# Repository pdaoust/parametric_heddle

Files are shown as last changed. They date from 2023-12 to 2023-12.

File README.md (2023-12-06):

# Parametric heddle

A set of OpenSCAD files for generating a weaving loom heddle suitable for 3D printing. This heddle fits nicely into the heddle braces of this [rigid heddle weaving loom on Thingiverse](https://www.thingiverse.com/thing:490467).

You can configure various things like:

* the thickness of the dowel that runs the length of the heddle
* the height of the entire heddle (fun fact: I created these files because the build volume of my printer was slightly too small for the original heddle in the above project)
* the thickness of the reed
* the height of the reed holes
* reed dent count (threads per inch)
* the length of a heddle screen in inches

This design is a bit different from the original:

* The reeds are centred in the panel, so you don't have to worry about whether the file you're printing is a left or a right.
* It's meant to be assembled without screws if you like -- instead, you print out dowel end-caps and pressure-fit them into the screens at the ends of the dowel. There are little notch/tongue fittings to keep the thing from swivelling on the dowel, and to hopefully provide a little more pressure-fitting. (Note that, by default, the end-caps are configured to also have American #3 countersunk screw holes so you can screw them together if you like.)
* Because it's parametric and goes together with pressure fittings, this design is explicitly meant to let you assemble and reassemble variable-dent heddles of whatever configuration you like. Two inches of six-dent followed by one inch of twelve-dent? Go for it!!!
* All pieces are completely symmetrical, so you don't need to generate left and right models.

## Usage

Just open up `heddle.scad`, scroll down to the line where it says to uncomment various lines in order to generate models, and hit F6!. There are preconfigured lines for a heddle screen panel, a top dowel cap, and a bottom dowel cap.

To configure things, read all the documentation in the comments. It's quite well-documented (if you find something doesn't make sense, please open up a GitHub issue!) The parameters you'll probably want to change are `heddle_height`, `reed_dent`, and `screen_inches`.

## Examples

A bottom dowel cap, with #3 screw hole and tongues to fit into the screen handle. This is sized to match the original heddle design, in which the bottom handle pokes out past the last reed by about 8mm.

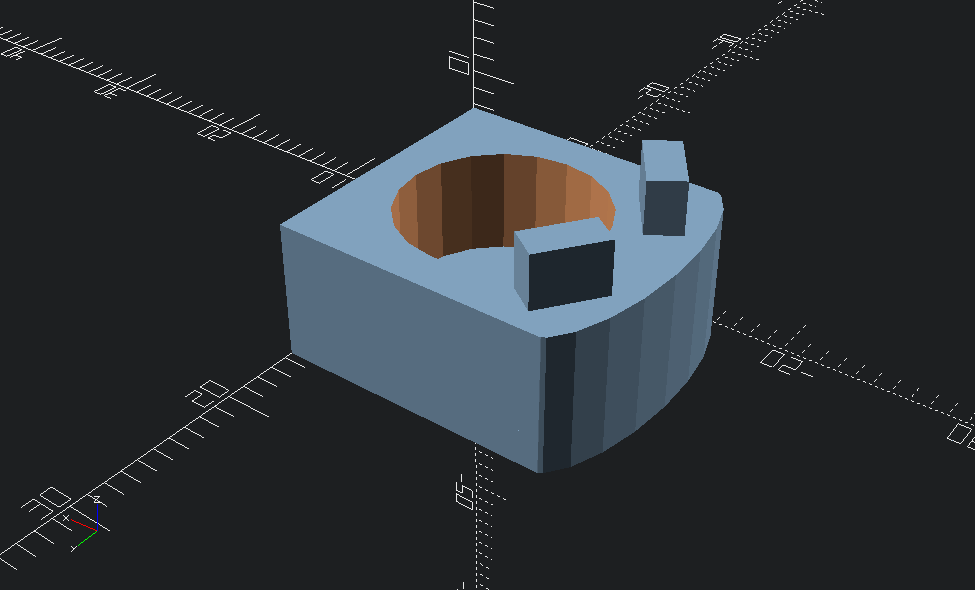
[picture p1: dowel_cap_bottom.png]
dowel cap bottom


A top dowel cap, which is basically just a thin panel with tongues and a screw hole. You might want to screw this one into the dowel if the pressure fitting isn't enough.

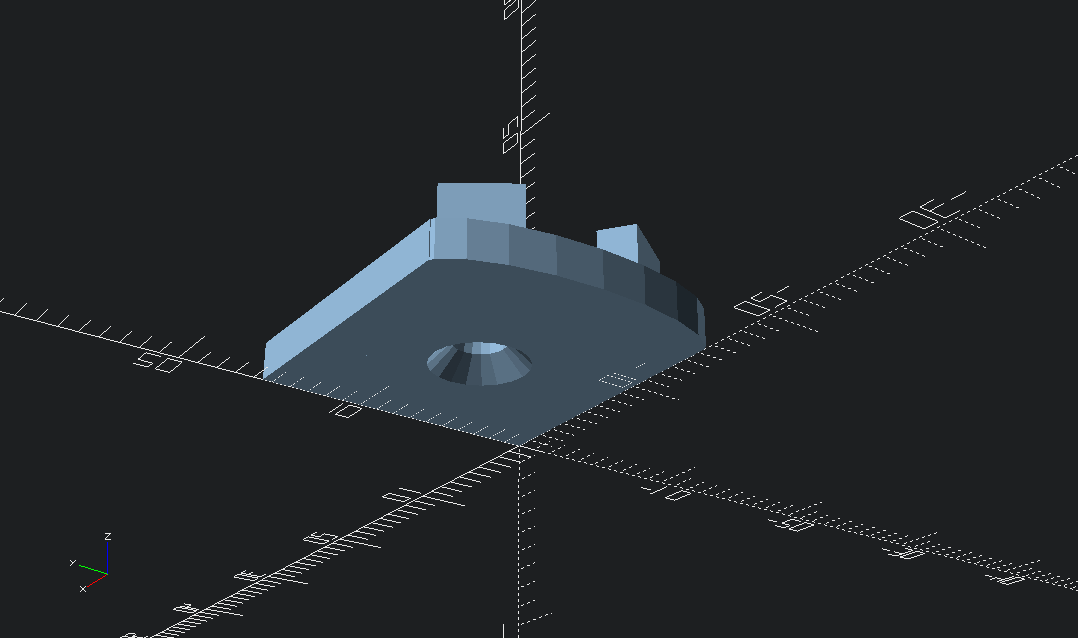
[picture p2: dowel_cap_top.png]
dowel cap top


A 12-dent screen four inches long.

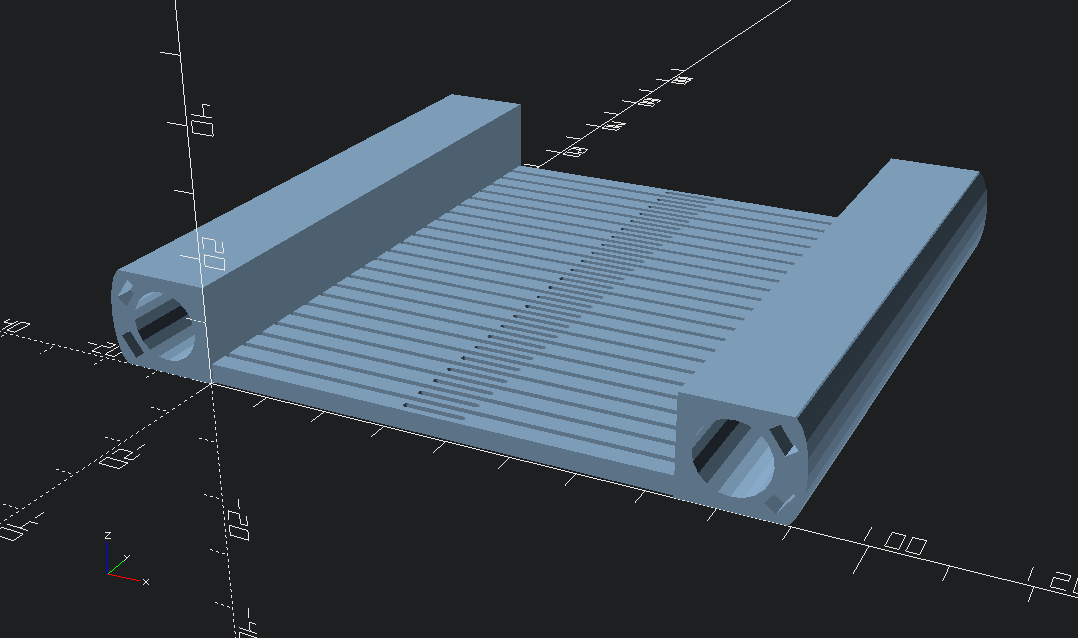
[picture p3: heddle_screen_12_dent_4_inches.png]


An 8-dent screen one inch long.

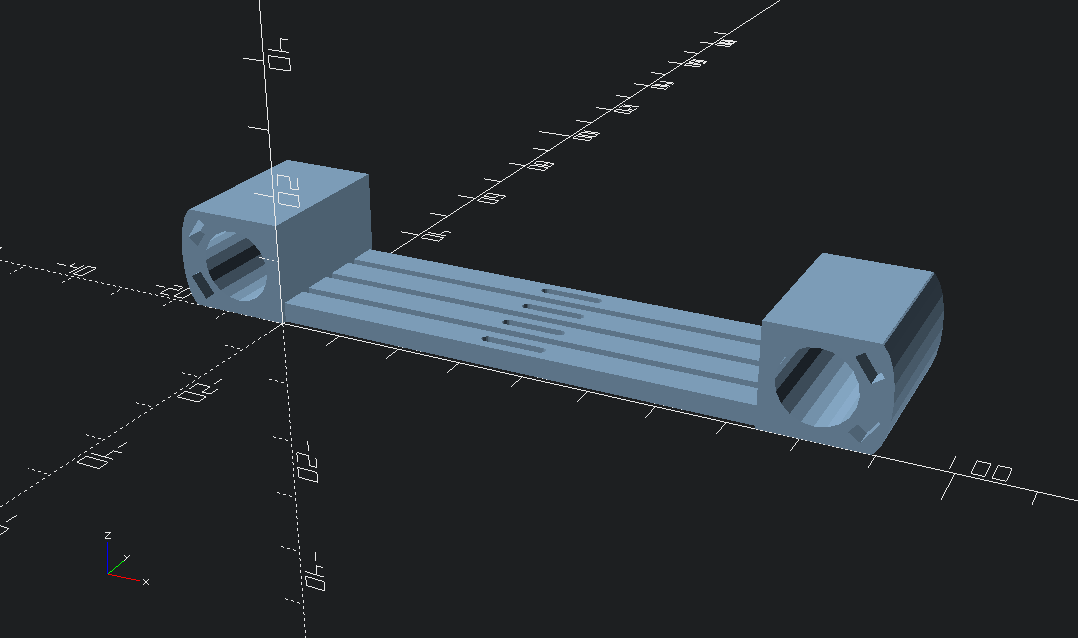
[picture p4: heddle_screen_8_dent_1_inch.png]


An 8-dent screen only 70mm tall and two inches long.

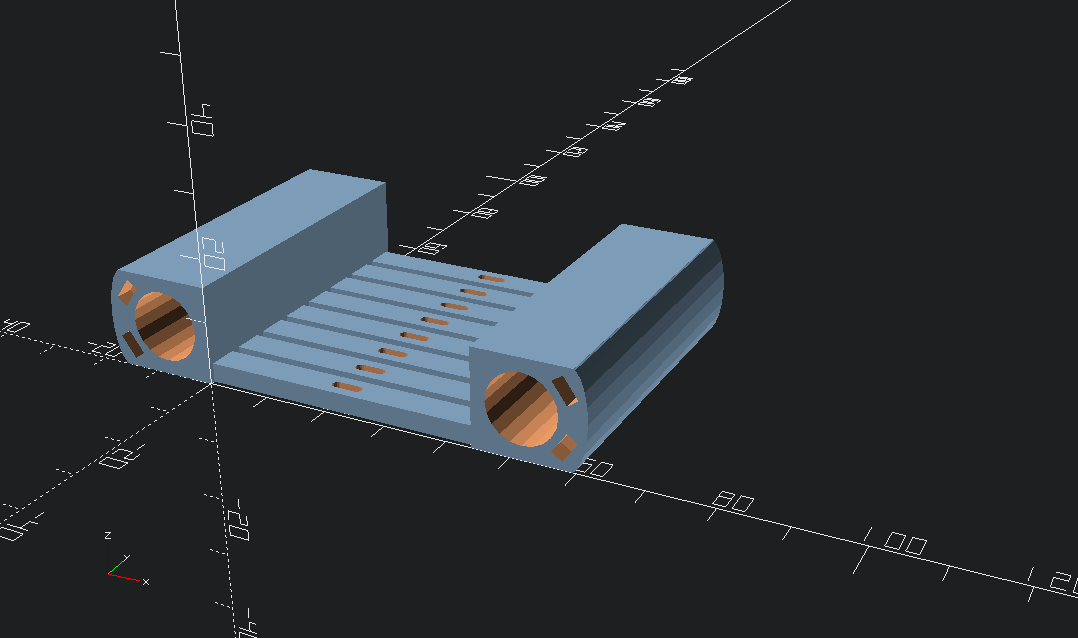
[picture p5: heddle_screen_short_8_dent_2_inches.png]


An 8-dent screen with a fancy band weaving pattern, similar to what you see in [this commercially available heddle](https://harvestlooms.com/products/15-double-slot-rigid-heddle-loom-weaving-backstrap-band-weaving-inkle-pattern-weaving-saami-sami-baltic-nordic-inlay-patterns).

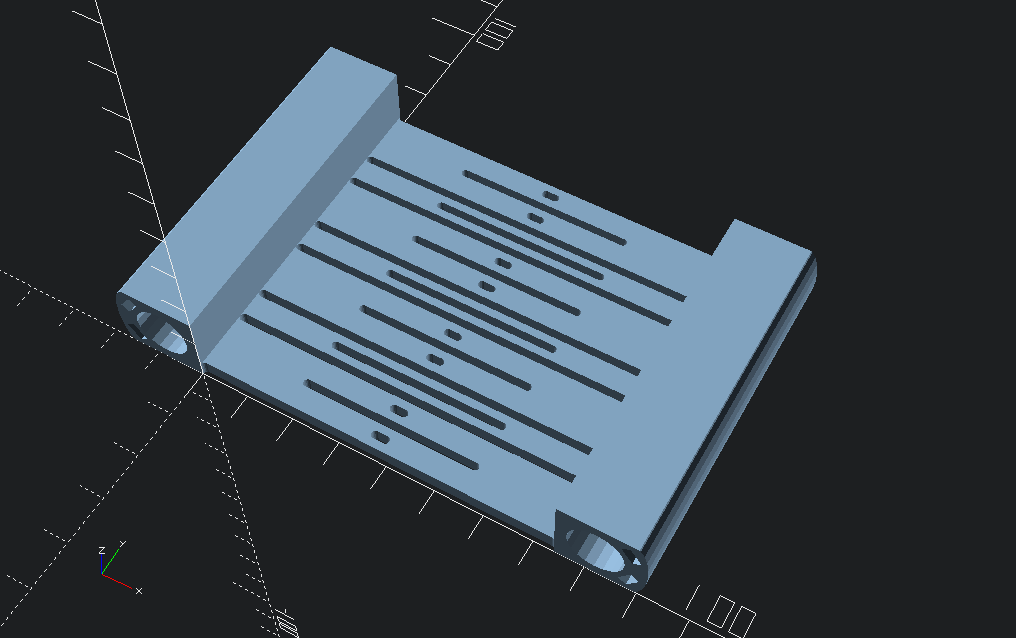
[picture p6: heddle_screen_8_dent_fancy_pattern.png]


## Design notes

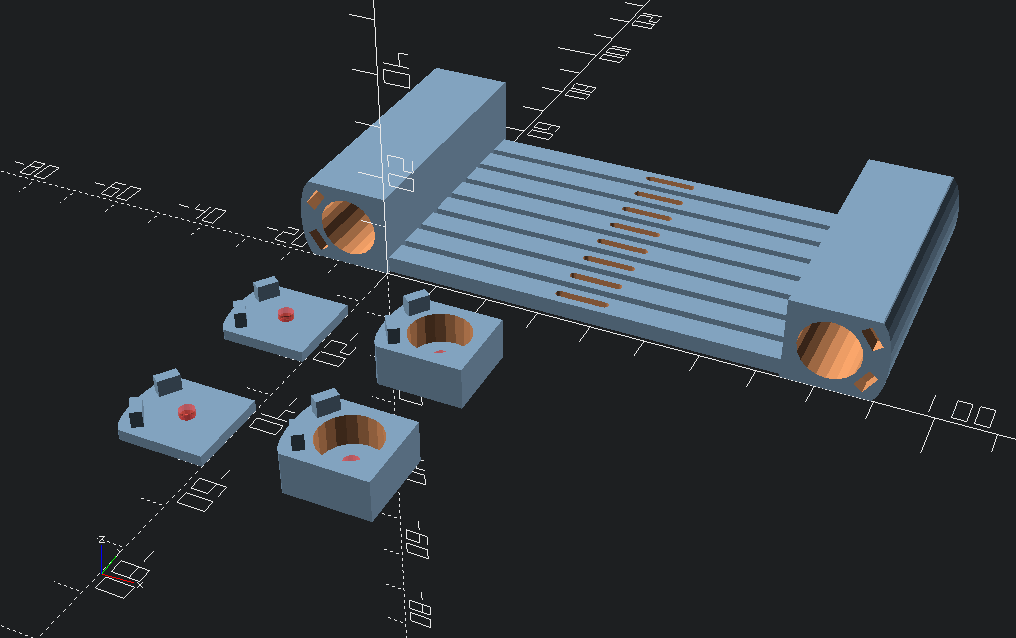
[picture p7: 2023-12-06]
heddle_pieces_example.png

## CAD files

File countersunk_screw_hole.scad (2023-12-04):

no_0_screw = [ .119 * 25.4, .06 * 25.4 ];
no_1_screw = [ .146 * 25.4, .073 * 25.4 ];
no_2_screw = [ 11/64 * 25.4, 3/32 * 25.4 ];
no_3_screw = [ 13/64 * 25.4, 7/64 * 25.4 ];
no_4_screw = [ 15/64 * 25.4, 7/64 * 25.4 ];
no_5_screw = [ 1/4 * 25.4, 1/8 * 25.4 ];
no_6_screw = [ 9/32 * 25.4, 9/64 * 25.4 ];
no_7_screw = [ 5/16 * 25.4, 5/32 * 25.4 ];
no_8_screw = [ 11/32 * 25.4, 5/32 * 25.4 ];
no_9_screw = [ 23/64 * 25.4, 11/64 * 25.4 ];
no_10_screw = [ 25/64 * 25.4, 3/16 * 25.4 ];
american_screw_sizes = [
  no_0_screw,
  no_1_screw,
  no_2_screw,
  no_3_screw,
  no_4_screw,
  no_5_screw,
  no_6_screw,
  no_7_screw,
  no_8_screw,
  no_9_screw,
  no_10_screw
];

function american_screw_size(number) = american_screw_sizes[number];

module countersunk_screw_hole(head_dia, shank_dia, shank_length) {
  head_depth = (head_dia - shank_dia) / 2;
  rotate([180, 0, 0]) union() {
    cylinder(head_depth, d1=head_dia, d2=shank_dia);
    translate([0, 0, head_depth - 0.001]) cylinder(shank_length, d=shank_dia);
  }
}

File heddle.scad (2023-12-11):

$fn = 40;

// The total height of the heddle from edge of bottom handle to edge
// of top handle. If you have a small printer, make sure this is
// equal to or less than the build volume dimension you're trying to
// fit it into.
// Fun fact: this default value is for my Monoprice Select Mini,
// whose build volume is just slightly smaller than the original
// RHL's screens. That's why I built this parameterised model in the
// first place!
heddle_height = 110;

// The thickness of all the reeds (not their width; that's calculated
// from the dent count).
reed_thickness = 3;

// The dent count, or number of threads per inch -- for example,
// 8-dent gives eight slots per inch to put threads through.
reed_dent = 8;

// Here's how you create patterns of holes and slots for the threads to fit
// through. The pattern is an array of lengths. Values that are less than
// or equal to 1 are treated as fractions of a full-length slot that goes
// all the way to the handles. Examples:
//
// * 1 = a slot that goes from the top to the bottom of the screen.
// * 0.1 = the hole is only 10% the height of the screen; the other 90%
//   is filled in.
//
// Values that are more than 1 are treated as lengths in millimetres. You
// may notice that this means you can't create an 1mm hole. That's tricky,
// because (a) you must have more dexterity than I do to thread something
// that thin, (b) your printer must have insanely good precision, and (c)
// the minimum hole length is the same as the hole width, which is
// calculated from the dent count:
//
//   hole width in inches = 1 ÷ dent count ÷ 2
//
// The pattern is repeated as many times as is necessary to fill up your
// reed panel, starting with a half-wide hole. I'd recommend a full slot
// for the first hole, because lining up two halves of a short hole might
// create alignment issues and sharp bits for the yarn to catch on.
// To see what I'm talking about, choose isometric view and look at it from
// directly above. See how the left and right edges of the screen are
// slightly narrower than than handles and have little scalloped corners?
// That's because they're both half of a slot.

// Here are some samples to get you going.

// An old-fashioned screen with nothing but full-length slots.
slots_reed_pattern = [1];

// A modern screen with alternating slots and holes.
slots_holes_reed_pattern = [1, 0.05];

// A fancy patterned screen for Sámi band weaving, similar to the ones
// made by Harvest Looms and Stoorstålka. Try it out on an 8-dent screen:
//
// * 1.75" will give you a 5-band heddle
// * 2.5" for a 7-band heddle
// * 3.5" for a 9-band heddle
//
// You need to sandwich the panel between two conventional slot-and-hole
// panels to complete the heddle.
band_weaving_reed_pattern_1 = [1, 0.5, 1, 0.05, 0.5, 0.05];

// Another popular patterned screen style for Sámi band weaving. This is
// meant to be assembled with one (or more) panel(s) on the left and
// identical one(s) on theright, but flipped, forming a mirror image.
// If you do 8-dent, make sure each panel is a multiple of 3/4" wide.
// Similarly for 12-dent, make it a multiple of 0.5" wide. Et cetera!
band_weaving_reed_pattern_2 = [1, 0.05, 0.333];

//// HEDDLE HANDLE SETTINGS

// These values affect the handles that run the top and bottom of the
// screens, as wel as the dowel caps that hold the assembly together.
// This design is different from ten16's original, in that the dowels are
// held in by end caps rather than screws (although you can choose to put
// screws into the end caps).

// The diameter of the dowel that runs the length of the heddle handles.
// Measure your dowel and change this value if it deviates from 7/16".
handle_dowel_dia = 7/16 * 25.4;

// For dowel caps, the thickness of the wall that supports the tongues
// and into which you screw an optional wood screw.
// FIXME: I don't know why it needs to be 0.001mm extra, but it does --
// otherwise the screw hole doesn't punch through the outside.
cap_wall_thickness = 2.001;

// A hole for a countersunk wood screw to attach the end caps to the dowel
// that runs through the handle of the entire heddle. You can choose an
// American screw number from countersunk_screw_hole_scad; I've commented
// out an example that uses a #3 screw.
// Keep this false if you just want to pressure-fit the end caps onto the
// dowels like I do.
include <countersunk_screw_hole.scad>;
//screw = no_3_screw;
screw = false;

// The bottom dowel caps are a bit longer than the top; this is so that
// they can reach all the way to the heddle brace. Adjust the length
// according to how much leftover space you expect to have after you've
// jammed a bunch of screen panels onto your bottom dowel. The default
// value matches that of the original design from ten16, although you'll
// have to cut your bottom dowels shorter by cap_wall_thickness × 2 to
// accommodate the dowel cap walls.
bottom_cap_length = 7.75;

// How much of a pressure fitting to put on the dowel caps. The total
// length of the top dowel caps will be this value plus the cap wall
// thickness (so you'll have to cut your top dowels this much longer than
// ten16's instructions), and the bottom dowel caps will just have a
// tighter bit of this length at the very end of the dowel holes (no
// adjustment needed here beyond what's described for the previous var).
// NOTE THAT this value can be zero if you're using a wood screw, in which
// case your top dowels can be the length that ten16 gives.
dowel_pressure_fitting_length = screw ? 0 : 4;

top_cap_length = cap_wall_thickness + dowel_pressure_fitting_length;

//// MORTISE AND TENON

// The dowel end caps need some way of locking into the panel of screen
// adjacent to them to prevent the whole dowel from rotating relative to
// the assembly. We use a little tongue and notch -- a mortise and tenon
// -- to make that happen. You don't need to worry about these settings
// unless you have troubles printing them and need to adjust.

// The dimensions of the mortise and tenon.
mortise_tenon_size = [4, 2, 2];

// The distance of the mortise and tenon from the non-curved end of the
// handle.
mortise_tenon_offset_from_base = -14.25;

// The gap between the two mortises and tenons.
mortise_tenon_spacing = 7;

// The fittings are rotated slightly for optimal fit between the
// dowel hole and the curved outer edge.
mortise_tenon_rotation = 55;

//// TOLERANCES

// Do some test prints with the default values (you can find some lines
// below to generate models for test prints) and twiddle these settings
// as needed. There are three places the tolerances are used:
//
// * The screen handles, into which the dowels go -- this should be loose
//   enough for the dowels to slide right through, but not so loose that
//   they wobble around sloppily.
// * The mortise-and-tenon joints in the dowel end caps -- these don't need
//   to be snug, and in fact shouldn't (I've had tenons break off). They
//   only need to be tight enough to not wobble around.
// * Pressure fittings in the dowel end caps -- if you're using screws, the
//   dowel holes in the end caps can be the same diameter as the ones in
//   the screen handles, but if you're using pressure fitting, they should
//   be snug.

// The gap between things that should fit snugly together.
pressure_fitting_tolerance = 0.15;

// The gap between things that should _not_ fit snugly together.
loose_tolerance = 0.3;

// The vagaries of 3D printing might mean you need to adjust the mortise
// and tenon tolerance separately from the dowel tolerance. You can adjust
// dowel tolerance by changing handle_dowel_dia, but changing
// mortise_tenon_size won't work the same, because it'll adjust both the
// mortises and tenons!
mortise_tenon_tolerance = loose_tolerance;

// Think of this as Cura's horizontal expansion setting, but you're
// expanding holes, not solids, and it's just for the holes that you slip
// the thread through.
reed_hole_expansion = 0.1;
 
//////// HERE'S WHERE YOU OUTPUT THE STUFF!

// Uncomment this line to build a whole screen panel. The first value is
// the width of the panel in mm (you can see I've specified it in inches
// then converted it to mm), while the second value is an array of hole
// sizes (see above for some examples). You can also override all the
// default values; see the screen() module below for parameter order.
//
// Keep in mind that you want your screen length to be some tidy multiple
// of the reeds you're specifying. For instance, a simple pattern of
// slots and holes in an 8-dent reed will repeat every 1/4 inch
// (1/8" hole spacing * 2 hole sizes in the pattern). So you'll want a
// screen length of some multiple of 1/4".
// The example given here uses the band weaving pattern to create a 7-band
// heddle panel to be used between two conventional slot-and-hole panels.
//panel(band_weaving_reed_pattern_1, 2.5 * 25.4);
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

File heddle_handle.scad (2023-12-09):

// For dowel caps, the thickness of the wall that supports the tongues
// and into which you screw a wood screw.
// FIXME: I don't know why I need it to be 0.001mm extra, but I do --
// otherwise the screw hole doesn't punch through the outside.
cap_wall_thickness = is_undef(cap_wall_thickness) ? 2.001 : cap_wall_thickness;

// The bottom caps are longer than the top caps, so the screen can
// reach all the way to the heddle brace. This is an approximation
// of the bottom cap lengths from the original design.
bottom_cap_length = 7.75;

// A hole for a countersunk wood screw to attach the handle caps
// to the dowel that runs through the handle of the entire heddle.
// Set this to false if you just want to pressure-fit the handle caps
// with the built-in tongues and notches.
// This setting applies only to dowel caps, not screen handles.
include <countersunk_screw_hole.scad>;
screw = is_undef(screw) ? no_3_screw : screw;

// The amount by which to expand holes and shrink tongues.
// Adjust this to match the precision of your printer.
pressure_fitting_tolerance = is_undef(pressure_fitting_tolerance) ? 0 : pressure_fitting_tolerance;

// By default this is a bit looser than the usual pressure fitting
// tolerance so you can slip screen panels on and off quickly.
dowel_hole_tolerance = is_undef(dowel_hole_tolerance) ? 0.015 : dowel_hole_tolerance;

// The dowel caps, however, look to the presence or absence of screw holes
// to decide whether to use the tight pressure fitting tolerance versus
// the loose dowel hole tolerance.
dowel_cap_hole_tolerance = screw ? dowel_hole_tolerance : pressure_fitting_tolerance;

// Within reason, you can play around with the dowel size.
// Make sure the handle walls are thick enough though!
handle_dowel_dia = is_undef(handle_dowel_dia) ? 7/16 * 25.4 : handle_dowel_dia;

// The size of the tongue and notch to attach the end caps to the
// dowel and the heddle screen panels. If you play with these values,
// make sure the handles have thick enough walls afterward!
mortise_tenon_size = is_undef(mortise_tenon_size) ? [4, 3, 2] : mortise_size;
mortise_tenon_offset_from_base = is_undef(mortise_tenon_offset_from_base) ? -14.25 : mortise_tenon_offset_from_base;

// This is the gap between the two fitting notches/tongues.
mortise_tenon_spacing = is_undef(mortise_tenon_spacing) ? 7 : mortise_tenon_spacing;

// The fittings are rotated slightly for optimal fit between the
// dowel hole and the curved outer edge.
mortise_tenon_rotation = 55;
mortise_tenon_tolerance = pressure_fitting_tolerance;

// If you want this to be compatible with the original loom's
// heddle block, treat the rest of the variables as constants.
handle_thickness = 15.5;

// This constant doesn't actually affect anything; it's just a rough
// eyeballing of the amount the curved end pokes out beyond the cube.
handle_bezel_height = 2.5;
handle_height = handle_thickness + handle_bezel_height;

handle_with_fittings("fitting-tolerance-test", 20);

module handle_with_fittings(style, length, screw = false) {  
  if (style == "screen") {
    difference() {
      handle(length);
      
      // The dowel hole.
      translate([handle_thickness / -2, -0.001, handle_thickness / 2]) rotate([-90, 0, 0]) cylinder(length + 0.002, d=handle_dowel_dia + dowel_hole_tolerance);

      translate([0, -0.001, 0]) mortise_tenon_cubes("notch");
      // I cannot for the life of me figure out where this 0.08 is coming from and why it's necessary.
      // Anyhow, a handle with notches needs them on both sides.
      translate([0, length - mortise_tenon_size.y + 0.08, 0]) mortise_tenon_cubes("notch");
    }
  } else if (style == "tolerance-test") {
    length = cap_wall_thickness + mortise_tenon_size.y + mortise_tenon_tolerance / 2;
    difference() {
      handle(length);
      translate([0, length - mortise_tenon_size.y + 0.08, 0]) mortise_tenon_cubes("notch");
      translate([handle_thickness / -2, -0.001, handle_thickness / 2]) rotate([-90, 0, 0]) cylinder(length + 0.002, d=handle_dowel_dia + loose_tolerance * 2);
    }
  } else {
    union() {
      handle(length);
      // A handle with tongues only needs one...
      translate([0, 0.001 - mortise_tenon_size.y, 0]) mortise_tenon_cubes("tongue");
      // Because the other end is just a cap.
      translate([-handle_thickness, length - cap_wall_thickness, 0]) difference() {
        cube([handle_thickness, cap_wall_thickness, handle_thickness]);
        if (screw) {
          // FIXME: not sure why the overlap has to be 0.01 instead of
          // 0.001 in order to work.
          translate([handle_thickness / 2, cap_wall_thickness + 0.01, handle_thickness / 2]) rotate([-90, 0, 0]) countersunk_screw_hole(screw[0], screw[1], cap_wall_thickness);
        }
      }
    }
  }
}

module mortise_tenon_cubes(component) {
  mortise_tenon_depth_offset = mortise_tenon_size.y / 2 - 0.001;
  offset = component == "notch" ? mortise_tenon_tolerance : -mortise_tenon_tolerance;
  size = [
    mortise_tenon_size.x + offset,
    mortise_tenon_size.y + offset / 2,
    mortise_tenon_size.z + offset
  ];
  translate([mortise_tenon_offset_from_base, mortise_tenon_depth_offset, mortise_tenon_spacing / 2]) rotate([0, mortise_tenon_rotation, 0]) cube(size, center=true);
  translate([mortise_tenon_offset_from_base, mortise_tenon_depth_offset, handle_thickness - mortise_tenon_spacing / 2]) rotate([0, -mortise_tenon_rotation, 0]) cube(size, center=true);
}

module handle(length) {
  translate([handle_thickness / -2, length / 2, handle_thickness / 2]) union() {
    translate([handle_thickness / -2 + 0.65, 0, 0]) intersection() {
      scale([0.35, 1, 1]) rotate([-90, 0, 0]) cylinder(length, d=16, center=true);
      cube([handle_thickness * 2, length, handle_thickness], center=true);
    }
    
    cube([handle_thickness, length, handle_thickness], center=true);
  }
}

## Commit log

2023-12-04 actual initial commit -- scad files
    [countersunk_screw_hole.scad, heddle.scad, heddle_handle.scad]
2023-12-05 add fitting_tolerance as overridable
    [heddle.scad]
2023-12-05 remove debug from screw hole
    [heddle_handle.scad]
2023-12-05 add tolerance test models
    [heddle.scad, heddle_handle.scad]
2023-12-05 change default screen to 2 inches
    [heddle.scad]
2023-12-06 fancy patterned reeds
    [heddle.scad]
2023-12-06 comment out fitting tolerance test models
    [heddle.scad]
2023-12-06 change recommendation for fancy heddle pattern example width
    [heddle.scad]
2023-12-06 code/documentation reorg -- specify screen length and heddle pattern in module call
    [heddle.scad]
2023-12-06 small note about pressure-fitting top dowel cap
    [heddle.scad]
2023-12-06 fix previous comment
    [cap and handle fitting test, zero tolerance.stl, example-fancy-patterned-heddle.stl, heddle.scad]
2023-12-08 add another Sámi band weaving pattern
    [heddle.scad]
2023-12-08 big reorg/rename of pressure fitting tolerances and mortise/tenon
    [heddle.scad, heddle_handle.scad]
2023-12-09 big huge refactor, better code reorg and settings
    [heddle.scad, heddle_handle.scad]
2023-12-09 fix default screen example width
    [heddle.scad]
2023-12-09 fix screw default
    [heddle-print-test.stl, heddle.scad]
2023-12-09 fix tolerance test example
    [heddle.scad]
2023-12-09 messy commit - refactor screen out, rename screen to panel, add spacer handle style
    [heddle.scad]
2023-12-10 increase tolerances
    [heddle.scad]
2023-12-10 add reed hole expansion, fix bug with tiny holes
    [heddle.scad]
2023-12-11 remove built files
    [cap and handle fitting test, zero tolerance.stl, example-fancy-patterned-heddle.stl, heddle-print-test.stl]
2023-12-11 shrink mortise/tenon depth
    [heddle.scad]
2023-12-11 clean up comments/examples
    [heddle.scad]
